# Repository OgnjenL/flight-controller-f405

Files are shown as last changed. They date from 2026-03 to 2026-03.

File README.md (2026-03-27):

# STM32F405RGT6 Drone Flight Controller

## Custom-designed 4-layer Flight Controller

This project focuses on PCB design around the STM32F405 MCU. It features a 4-layer PCB with dedicated ground and power planes with an integrated IMU.

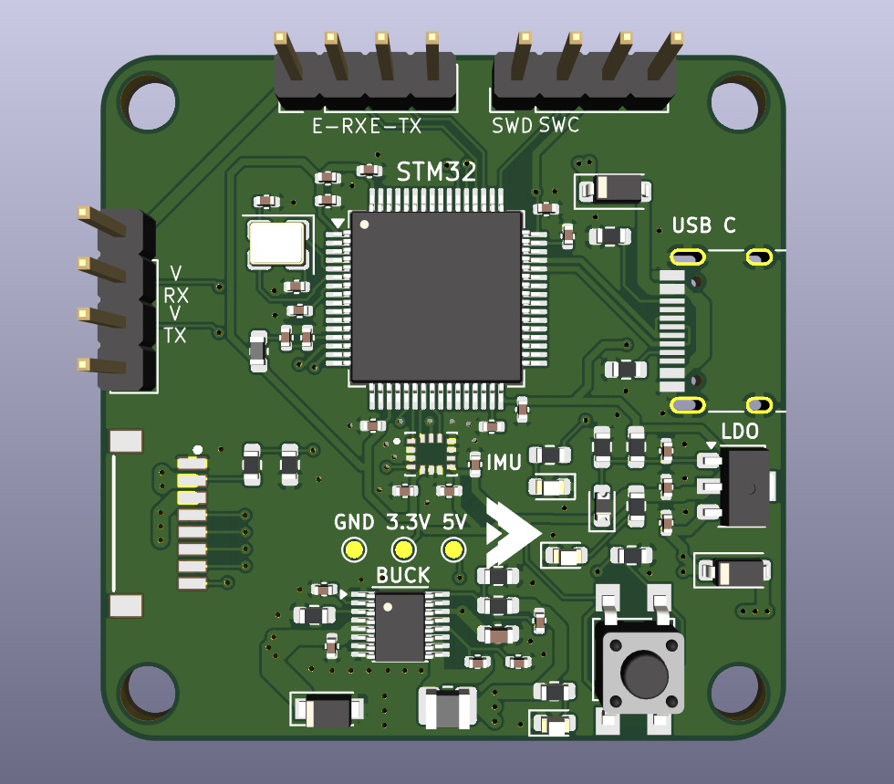
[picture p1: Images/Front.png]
Front view

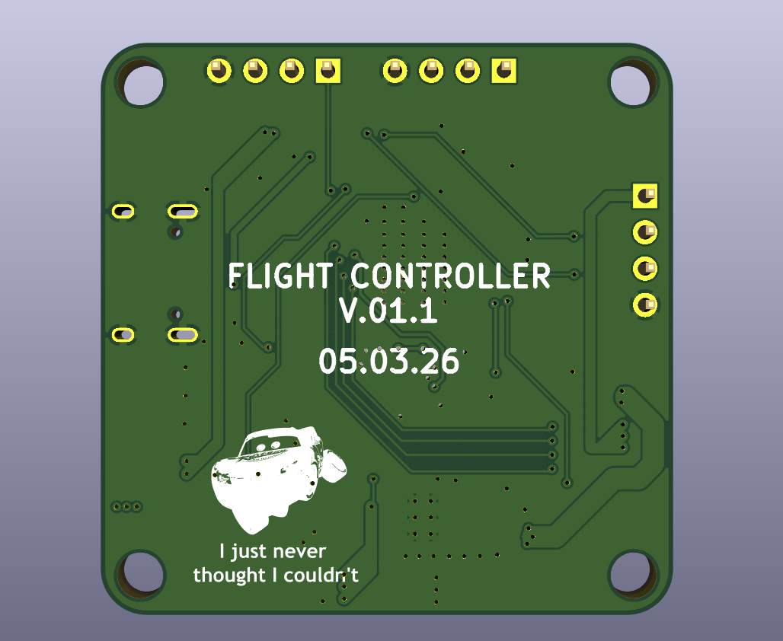
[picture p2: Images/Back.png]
Back view


### Components and Specifications

* Microcontroller: STM32F405RGT6
* IMU: ICM-42670-P
* Power Management: 5V BUCK - LT8610, 3.3V LDO - LT1117-ADJ

The board is designed according to JLCPCB's manufacturing constraints, and the BOM is for LCSC parts.

1.  **Fabrication:** Upload the **V01.2_2.zip** file from the '/production' folder. Use a **4-layer** setting and a **1.6mm** board thickness.
2.  **Sourcing:** Use the provided **V01.2_2_bom.csv** file from the '/production' folder for automated part sourcing.
3.  **Assembly:** Reference the **V01.2_2_positions** file from the '/production' folder if using SMT assembly services, or use the silkscreen markings for manual soldering.
4.  **Datasheets:** STM32F405RGT6 - [stm32f405rg.pdf](https://github.com/user-attachments/files/26315604/stm32f405rg.pdf)
                    LT8610 - [LT8610 - datasheet.pdf](https://github.com/user-attachments/files/26315737/LT8610.-.datasheet.pdf)
                    LT1117 - [LT1117.PDF](https://github.com/user-attachments/files/26315667/LT1117.PDF)
                    ICM-42670-p - [ICM-42688-P.PDF](https://github.com/user-attachments/files/26315769/ICM-42688-P.PDF)

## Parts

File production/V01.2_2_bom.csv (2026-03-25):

Designator | Quantity | LCSC Part #
BUCK | 1 | C462619
C1, C12, C13, C17, C2, C23, C24, C3, C4, C5, C9 | 11 | C60474
C10, C19, C22 | 3 | C60133
C11, C7, C8 | 3 | C170151
C14, C15, C6 | 3 | C315248
C16, C18, C25 | 3 | C713505
C21 | 1 | C6119795
C26 | 1 | C178330
D1, D2 | 2 | C5345968
D3, D4, D5 | 3 | C19273151
D6 | 1 | C478011
D8 | 1 | C30584800
FB1 | 1 | C107335
J1 | 1 | C165948
J2 | 1 | C265120
L1 | 1 | C39846710
LDO | 1 | C3014296
MT1 | 1 | C3288646
R1, R4 | 2 | C98220
R10 | 1 | C2906984
R11 | 1 | C49654438
R12 | 1 | C2907115
R13, R7, R9 | 3 | C2907148
R2, R3 | 2 | C2907044
R5 | 1 | C2907123
R6 | 1 | C2933134
R8 | 1 | C2907113
STM32 | 1 | C15742
SW1 | 1 | C2886902
Y1 | 1 | C2916927

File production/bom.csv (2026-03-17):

Designator | Footprint | Quantity | Value | LCSC Part #
BUCK | MSOP-16-1EP_3x4.039mm_P0.5mm_EP1.651x2.845mm_ThermalVias | 1 | LT8610 | C462619
C1, C12, C13, C17, C2, C23, C24, C3, C4, C5, C9 | 201 | 11 | 100n | C49062
C10, C19, C22 | 201 | 3 | 10n | C76941
C11, C7, C8 | 201 | 3 | 2.2u | C318539
C14, C15, C6 | 402 | 3 | 10u | C315248
C16, C18, C25 | 201 | 3 | 10p | C43535
C21 | 402 | 1 | 4.7u | C6119795
C26 | 603 | 1 | 47u | C178330
D1, D2 | D_SOD-123 | 2 | D_Schottky | C5345968
D3, D4, D5 | 603 | 3 | LED | C19273151
D6 | D_SMA | 1 | D_TVS | C49207092
D8 | 603 | 1 | D | C30584800
FB1 | 603 | 1 | FerriteBead | C107335
J1 | USB_C_Receptacle_HRO_TYPE-C-31-M-12 | 1 | USB_C_Receptacle_USB2.0_14P | C165948
J2 | JST_SM08B-SRSS-TB_LF__SN_ | 1 | Conn_01x08_Socket | C265120
L1 | 805 | 1 | 10u | C48944993
LDO | SOT-89-3 | 1 | LT1117-ADJ | C3014296
MT1 | XDCR_ICM-42670-P | 1 | ICM-42670-P | C3288646
R1, R4 | 603 | 2 | 10k | C98220
R10 | 603 | 1 | 110k | C2906984
R11 | 603 | 1 | 243k | C137764
R12 | 603 | 1 | 1Meg | C2907115
R13, R7, R9 | 603 | 3 | 300 | C2907148
R2, R3 | 603 | 2 | 5.1k | C2907044
R5 | 603 | 1 | 200 | C25804
R6 | 603 | 1 | 121 | C2933134
R8 | 603 | 1 | 1k | C2907113
STM32 | LQFP-64_7x7mm_P0.4mm | 1 | STM32F405RGT6 | C15742
SW1 | SW_SPST_TL3305A | 1 | SW_Push | C2886902
Y1 | Crystal_SMD_3225-4Pin_3.2x2.5mm | 1 | Crystal_GND24 | C2916927

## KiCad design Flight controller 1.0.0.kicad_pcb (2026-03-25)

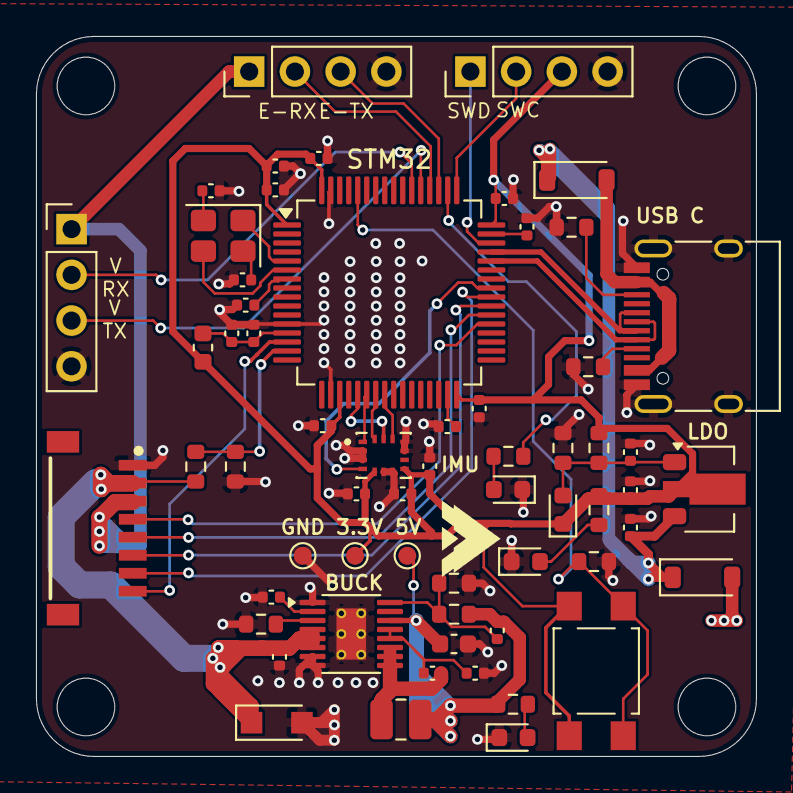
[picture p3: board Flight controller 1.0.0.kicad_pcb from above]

Board: 4 copper layers, 40.0 x 40.0 mm, 61 parts (0 on the bottom side), 46 nets.

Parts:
3.3V: 3.3V; TestPoint_Pad_D1.0mm
5V: 5V; TestPoint_Pad_D1.0mm
BUCK: LT8610; MSOP-16-1EP_3x4.039mm_P0.5mm_EP1.651x2.845mm_ThermalVias
C1, C2, C3, C4, C5, C9, C12, C13, C17, C23, C24: 100n; C_0402_1005Metric
C6, C14, C15: 10u; C_0402_1005Metric
C7, C8, C11: 2.2u; C_0402_1005Metric
C10, C19, C22: 10n; C_0402_1005Metric
C16, C18, C25: 10p; C_0402_1005Metric
C21: 4.7u; C_0402_1005Metric
C26: 47u; C_0603_1608Metric
D1, D2: D_Schottky; D_SOD-123
D3, D4, D5: LED; LED_0603_1608Metric
D6: D_TVS; Nexperia_CFP3_SOD-123W
D8: D; D_0603_1608Metric
FB1: FerriteBead; L_0603_1608Metric
GND: GND; TestPoint_Pad_D1.0mm
J1: USB_C_Receptacle_USB2.0_14P; USB_C_Receptacle_HRO_TYPE-C-31-M-12
J2: Conn_01x08_Socket; JST_SM08B-SRSS-TB_LF__SN_
J3: Conn_01x04_Pin; PinHeader_1x04_P2.54mm_Vertical
J4, J5: Conn_01x04; PinHeader_1x04_P2.54mm_Vertical
L1: 10u; L_1008_2520Metric
LDO: LT1117-ADJ; SOT-89-3
MT1: ICM-42670-P; XDCR_ICM-42670-P
R1, R4: 10k; R_0603_1608Metric
R2, R3: 5.1k; R_0603_1608Metric
R5: 200; R_0603_1608Metric
R6: 121; R_0603_1608Metric
R7, R9, R13: 300; R_0603_1608Metric
R8: 1k; R_0603_1608Metric
R10: 110k; R_0603_1608Metric
R11: 243k; R_0603_1608Metric
R12: 1Meg; R_0603_1608Metric
STM32: STM32F405RGT6; LQFP-64_10x10mm_P0.5mm
SW1: SW_Push; SW_SPST_TL3305A
Y1: Crystal_GND24; Crystal_SMD_3225-4Pin_3.2x2.5mm

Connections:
+3.3V: 3.3V.1, C1.1, C2.1, C3.1, C4.1, C5.1, C6.1, C10.2, C11.2, C12.2, C15.1, D8.1 (K), FB1.1, J3.3, LDO.2 (VO), MT1.5 (VDDIO), MT1.8 (VDD), R6.1, R7.1, STM32.1 (VBAT), STM32.19 (VDD), STM32.32 (VDD), STM32.48 (VDD), STM32.64 (VDD), SW1.1
+5V: C13.1, D1.1 (K), D2.1 (K), LDO.3 (VI)
+5V_BUCK: 5V.1, BUCK.14 (BIAS), C25.2, C26.2, D2.2 (A), J2.3, J4.1, J5.1, L1.2, R12.2, R13.1
+5V_USB: D1.2 (A), J1.A4 (VBUS), J1.A9 (VBUS), J1.B4 (VBUS), J1.B9 (VBUS)
/+5V_BUCK_1: BUCK.9 (SW), BUCK.10 (SW), BUCK.11 (SW), C24.1, L1.1
/BOOT0: R1.2, STM32.60 (BOOT0), SW1.2
/CC1: J1.A5 (CC1), R3.1
/CC2: J1.B5 (CC2), R2.1
/LED_STM32: R9.1, STM32.50 (PA15)
/NRST: C9.1, STM32.7 (NRST)
/RCC_OSC_IN: STM32.5 (PH0), Y1.1
/RCC_OSC_OUT: STM32.6 (PH1), Y1.3
/TR/SS: BUCK.2 (TR/SS), C22.2
/VCAP1: C7.2, STM32.31 (VCAP_1)
/VCAP2: C8.2, STM32.47 (VCAP_2)
/VDDA: C17.1, C19.1, FB1.2, STM32.13 (VDDA)
Batt_control: R4.2, R8.1, STM32.15 (PA1)
Curr_sensor: J2.8, STM32.14 (PA0)
D+: J1.A6 (D+), J1.B6 (D+), STM32.45 (PA12)
D-: J1.A7 (D-), J1.B7 (D-), STM32.44 (PA11)
ELRS_RX: J5.2, STM32.52 (PC11)
ELRS_TX: J5.3, STM32.51 (PC10)
GND: BUCK.1 (SYNC), BUCK.7 (GND), BUCK.8 (GND), BUCK.17 (GND), C1.2, C2.2, C3.2, C4.2, C5.2, C6.2, C7.1, C8.1, C9.2, C10.1, C11.1, C12.1, C13.2, C14.2, C15.2, C16.1, C17.2, C18.1, C19.2, C21.2, C22.1, C23.2, C26.1, D3.1 (K), D4.1 (K), D5.1 (K), D6.2 (A2), GND.1, J1.A1 (GND), J1.A12 (GND), J1.B1 (GND), J1.B12 (GND), J1.S1 (SHIELD), J2.1, J3.4, J4.4, J5.4, MT1.2 (RESV), MT1.3 (RESV), MT1.6 (GND), MT1.7 (FSYNC), MT1.10 (RESV), MT1.11 (RESV), R1.1, R2.2, R3.2, R5.2, R8.2, R10.2, R11.2, STM32.12 (VSSA), STM32.18 (VSS), STM32.63 (VSS)
Interrupt: MT1.4 (INT1/INT), STM32.41 (PA8)
M1: J2.4, STM32.37 (PC6)
M2: J2.5, STM32.38 (PC7)
M3: J2.6, STM32.39 (PC8)
M4: J2.7, STM32.40 (PC9)
unnamed: C16.2, Y1.4
unnamed: C18.2, Y1.2
unnamed: D3.2 (A), R7.2
unnamed: D4.2 (A), R9.2
unnamed: D5.2 (A), R13.2
unnamed: C14.1, D8.2 (A), LDO.1 (ADJ), R5.1, R6.2
unnamed: BUCK.12 (BST), BUCK.13 (INTVcc), C23.1, C24.2
unnamed: BUCK.16 (FB), C25.1, R11.1, R12.1
unnamed: BUCK.3 (RT), R10.1
SPI1_CS: MT1.12 (AP_CS), STM32.24 (PC4)
SPI1_MISO: MT1.1 (AP_SDO/AP_AD0), STM32.22 (PA6)
SPI1_MOSI: MT1.14 (AP_SDA/AP_SDIO/AP_SDI), STM32.23 (PA7)
SPI1_SCK: MT1.13 (AP_SCL/AP_SCLK), STM32.21 (PA5)
SWCLK: J3.2, STM32.49 (PA14)
SWDIO: J3.1, STM32.46 (PA13)
VBat: BUCK.4 (EN/UV), BUCK.5 (VIN), BUCK.6 (VIN), C21.1, D6.1 (A1), J2.2, R4.1
VTX_RX: J4.2, STM32.54 (PD2)
VTX_TX: J4.3, STM32.53 (PC12)

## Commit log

2026-03-11 Initial commit: Konacna verzija
    [Flight controller 1.0.0-B_Cu.gbl, Flight controller 1.0.0-B_Mask.gbs, Flight controller 1.0.0-B_Paste.gbp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]
2026-03-17 Povecane komponente
    [Flight controller 1.0.0-B_Cu.gbl, Flight controller 1.0.0-B_Mask.gbs, Flight controller 1.0.0-B_Paste.gbp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]
2026-03-25 Update .gitignore and removing unwanted files
    [Flight controller 1.0.0-B_Cu.gbl, Flight controller 1.0.0-B_Mask.gbs, Flight controller 1.0.0-B_Paste.gbp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]
2026-03-27 Update README with project details and specifications
    Added detailed project description, components, and specifications for the STM32F405RGT6 Drone Flight Controller.
